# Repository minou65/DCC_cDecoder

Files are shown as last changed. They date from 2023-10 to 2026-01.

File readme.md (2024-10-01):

# cDecoder
## Inhalt
- [cDecoder](#cdecoder)
  - [Inhalt](#inhalt)
  - [Funktionen](#funktionen)
  - [Programmierung](#programmierung)
  - [Analog Betrieb](#analog-betrieb)
  - [Immer ein](#immer-ein)
  - [Powerpack](#powerpack)
  - [Dimmen der Ausgänge](#dimmen-der-ausgänge)
  - [Anschlüsse](#anschlüsse)
    - [fDecoder](#fdecoder)
    - [cDecoder](#cdecoder-1)
    - [PowerPack](#powerpack-1)
    - [Farben](#farben)
  - [Lange DCC Adresse](#lange-dcc-adresse)
  - [CV Tabelle](#cv-tabelle)
    - [Zuordnung Ausgänge zu Funktionstasten](#zuordnung-ausgänge-zu-funktionstasten)
    - [Funktion aktiv bei](#funktion-aktiv-bei)
    - [Modus der Ausgänge](#modus-der-ausgänge)
      - [Blinker On Time](#blinker-on-time)
      - [Blinker off Time](#blinker-off-time)
      - [Dimmen der Ausgänge](#dimmen-der-ausgänge-1)
      - [Automatisches abschalten](#automatisches-abschalten)
  - [Beispiele](#beispiele)
  - [Programmieren des prozessors](#programmieren-des-prozessors)

## Funktionen
- Ein/Aus
- Impuls
- Blinker

Der Attiny85 untersützt nur 5 Ausgänge. Die Funktionen sind auf die Ausgänge verteilt. Die Funktionen können über die CV's 66 - 70 eingestellt werden. 
Die Blinkerfunktion kann über die CV's 71 - 75 eingestellt werden. Die Zeit für das Blinken kann über die CV's 76 - 80 eingestellt werden. 
Die Zeit wird in 10ms Schritten angegeben. Die Helligkeit der Ausgänge kann über die CV's 81 und 82 eingestellt werden. 
Die Zeit für das automatische abschalten kann über die CV's 86 - 90 eingestellt werden. Die Zeit wird in 10ms Schritten angegeben.

## Programmierung
Um den Decoder auf dem Programmiergleis programmieren zu können muss eine Last an AUX 1 angeschlossen werden, die mindestens einen Strom von 60mA erzeugt.

## Analog Betrieb
Wird während 100ms kein DCC Signal erkannt, werden die Funktionen gemäss CV 13 aktiviert

## Immer ein
Ab Version 3 untersützt die Firmware CV 123, damit können Ausgänge definiert werden, welche beim anlagen einer Spannung sofort eingeschaltet werden.
Eingeführt für die Rheinbrücke beim Modell Eisenbahn Club Seebezirk (MECS), Fräschels (CH)

## Powerpack
Ein externes Powerpack kann an den Decoder angeschlossen werden. Dazu können die Pad's VCC und GND auf der Rückseite des Decoders verwendet werden.

## Dimmen der Ausgänge
Die Ausgänge AUX 1 und AUX 2 können gedimmt werden. Die Helligkeit kann über CV 81 und 82 eingestellt werden.

## Anschlüsse
### fDecoder
| oben | unten |
|---|---|
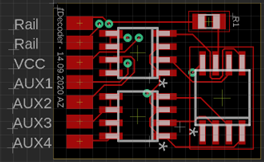
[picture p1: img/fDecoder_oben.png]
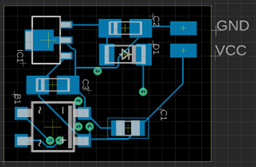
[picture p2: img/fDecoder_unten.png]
|  |  |
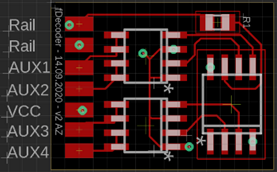
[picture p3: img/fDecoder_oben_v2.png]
| __v2__ <br>  | |

### cDecoder
| oben | unten |
|---|---|
| ||

### PowerPack
| oben | unten |
|---|---|
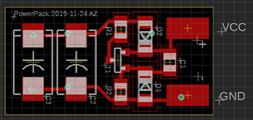
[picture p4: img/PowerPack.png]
|  ||

### Farben
| Draht | Verwendung |
|---|---|
| Rot | Rail |
| Braun | Rail |
| Blau | Decoder + |
| Weiss | Aux 1 / Licht vorne |
| Gelb | Aux 2 / Licht hinten |
| Violett | Aux 3 |
| Grün | Aux 4 |
| Schwarz | GND |

## Lange DCC Adresse
Um die lange DCC-Adresse in die Register 17 und 18 umzurechnen, kann folgende Formel verwendet werden.<br><br>
CV 17 = Adresse / 256 (nur die Stellen vor dem Komma) + 192<br>
CV 18 = Adresse - ((CV 17 - 192) * 256)<br>

Die lange Adresse wird nur verwendet, wenn das Bit 5 in CV 29 gesetzt ist

Hier gibt es einen CV Rechner
https://www.opendcc.de/info/decoder/dcc_cv.html

## CV Tabelle
| Bezeichnung | CV | Wertbereich <br> (default) | Beschreibung |
|---|:---:|---|---|
| Basisadresse | 1 | 1 - 255 (3) | Wertebereich im DCC-Format 1 - 127 |
| | 2 | 120 | |
| | 5 | 255 | |
| Version | 7 | | |
| Hersteller | 8 | | |
| Reset | 8 |  | Durch Eingeben eines Wertes 8, werden alle Einstellungen auf Default gesetzt |
| Im Analogbetrieb aktive Ausgänge | 13 | 0 - 255 (0) | AUX 1 ein = 1<br>AUX 2 ein = 2<br>AUX 3 ein = 4<br>AUX 4 ein = 8<br>AUX 5 ein = 16 |
| Decoderlock | 15 | 0 - 255 (0) | Decoder-Lock Funktion laut NMRA. <br>Details siehe http://www.nmra.org/standards/DCC/WGpublic/0305051/0305051.html |
| Decoderlock | 16 | 0 - 255 (0) | Decoder-Lock Funktion laut NMRA. <br>Details siehe http://www.nmra.org/standards/DCC/WGpublic/0305051/0305051.html |
| Erweiterte Adresse | 17 | 192 - 255 (0) | Nur für DCC-Format. Bei den meisten Zentralen ist es möglich, <br> erweiterte Adressendirekt einzugeben. Die CVs 17, 18 und 29 <br> werden von der Zentrale automatisch richtig eingestellt. |
| Erweiterte Adresse | 18 | 0 - 255 (3) |
| Konfigurationsdaten | 29 | 0 - 64 (2) | Fahrtrichtung Standard = 0 <br>Fahrtrichtung invertiert = 1 <br>14 Fahrstufen = 0 <br>28 oder 128 Fahrstufen 2 <br>Basisadressen = 0 <br>Erweiterte Adressen = 32 |
| Betriebszustand | 122 | 0/1 (0) | Den Betriebszustand der Ausgänge speichern. <br>0 = Aus <br>1 = Ein |
| Immer eingeschaltet<br>(ab Version 3) | 123 | 0 - 255 (0) | AUX 1 ein = 1<br>AUX 2 ein = 2<br>AUX 3 ein = 4<br>AUX 4 ein = 8<br>AUX 5 ein = 16 |

### Zuordnung Ausgänge zu Funktionstasten
| Bezeichnung | CV | Wertbereich <br> (default) | Beschreibung |
|---|:---:|---|---|
| F0 | 30 | 0 - 31 (3) | AUX 1 = 1 <br> AUX 2 = 2 <br> AUX 3 = 4 <br> AUX 4 = 8 <br> AUX 5 = 16 |
| F1 | 31 | 0 - 31 (4) | |
| F2 | 32 | 0 - 31 (8) | |
| ... | ... | 0 - 31 (0) | |
| F28 | 58 | 0 - 31 (0) | |

### Funktion aktiv bei
| Bezeichnung | CV | Wertbereich <br> (default) | Beschreibung |
|---|:---:|---|---|
| AUX 1 | 61 | 0 - 31 (1) | Vorwärts = 0 <br> Rückwärts = 1 <br> Beide = 3 <br> Default bei cDecoder ist 3 |
| AUX 2 | 62 | 0 - 31 (2) | Default bei cDecoder ist 3 |
| AUX 3 | 63 | 0 - 31 (3) | |
| AUX 4 | 64 | 0 - 31 (3) | |
| AUX 5 | 65 | 0 - 31 (3) | |

### Modus der Ausgänge
| Bezeichnung | CV | Wertbereich <br> (default) | Beschreibung |
|---|:---:|---|---|
| AUX 1 | 66 | 0 - 31 (1) | Ein / Aus = 1 <br> Blinker = 2 <br> Impuls = 3 |
| AUX 2 | 67 | 0 - 31 (1) | |
| AUX 3 | 68 | 0 - 31 (1) | |
| AUX 4 | 69 | 0 - 31 (2) | |
| AUX 5 | 70 | 0 - 31 (2) | |

#### Blinker On Time
| Bezeichnung | CV | Wertbereich <br> (default) | Beschreibung |
|---|:---:|---|---|
| AUX 1 | 71 | 0 - 255 (100) | Wert x 10 = Zeit in milli Sekunden |
| AUX 2 | 72 | 0 - 255 (100) | |
| AUX 3 | 73 | 0 - 255 (100) | |
| AUX 4 | 74 | 0 - 255 (100) | |
| AUX 5 | 75 | 0 - 255 (100) | |

#### Blinker off Time
| Bezeichnung | CV | Wertbereich <br> (default) | Beschreibung |
|---|:---:|---|---|
| AUX 1 | 76 | 0 - 255 (100) | Wert x 10 = Zeit in milli Sekunden |
| AUX 2 | 77 | 0 - 255 (100) | |
| AUX 3 | 78 | 0 - 255 (100) | |
| AUX 4 | 79 | 0 - 255 (100) | |
| AUX 5 | 80 | 0 - 255 (100) | |

#### Dimmen der Ausgänge
| Bezeichnung | CV | Wertbereich <br> (default) | Beschreibung |
|---|:---:|---|---|
| AUX 1 | 81 | 1 - 255 (255) | |
| AUX 2 | 82 | 1 - 255 (255) | |

#### Automatisches abschalten
| Bezeichnung | CV | Wertbereich <br> (default) | Beschreibung |
|---|:---:|---|---|
| AUX 1 | 86 | 0 - 255 (0) | Wert x 10 = Zeit in milli Sekunden. Ist der <br> Wert grösser als 0 wird der Ausgang nach der <br> eingestellten Zeit wieder abgeschaltet. <br> Ist der Wert 0, dann bleibt der Ausgang eingeschaltet. |
| AUX 2 | 87 | 0 - 255 (0) | |
| AUX 3 | 88 | 0 - 255 (0) | |
| AUX 4 | 89 | 0 - 255 (0) | |
| AUX 5 | 90 | 0 - 255 (0) | |

## Beispiele
|Beispiel | Einstellungen |
|---|---|
| SBB Schlusslicht an AUX 4 <br><br><br><br> | CV64 = 36<br>CV69 = 27 <br>CV74 = 1 (On Time)<br>CV79 = 70 (Off Time) |
| Rheinbrücke MESC<br>Rote LED soll immer blinken<br><br><br> | CV123 = 1<br>CV66 = 2<br>CV71 = 80<br>76 = 20 |

## Programmieren des prozessors

Um den Prozessor zu programmieren wird ein ISP Programmer benötigt. Der Prozessor kann mit der Arduino IDE programmiert werden. Dazu muss der Prozessor als Board hinzugefügt werden.
- Dazu unter Datei -> Voreinstellungen -> Zusätzliche Boardverwalter-URLs: https://raw.githubusercontent.com/damellis/attiny/ide-1.6.x-boards-manager/package_damellis_attiny_index.json einfügen.
- Arduino AVR Boards installieren unter Werkzeuge -> Board -> Boardverwalter... -> Arduino AVR Boards installieren.
- In der Arduino IDE unter Werkzeuge -> Board -> Boardverwalter... -> attiny auswählen und installieren. 

Danach das Board wie folgt konfigurieren
    Board    : Attiny25/45/85
    Prozessor: Attiny85
    Clock    : Internal 16Mhz
    Programmer: Diamex USB ISP oder ATMEL STK500 (Für Windows 10 ist kein Treiber erforderlich)

Nun kann zuerst der Bootloader und danach die Firmware auf den Prozessor geschrieben werden. Unter visual Micro kommt folgende Fehlermeldung beim schreiben des Bootloaders

```
Error while burning bootloader.
Burn failed
avrdude: can't open input file aders/{bootloader.file}: No such file or directory
avrdude: read from file oaders/{bootloader.file}' failed
```

Dies ist normal, der Attiny hat keine Bootloader visual Micro sucht diesen aber und findet ihn nicht. Die Fuse und Clock settings werden aber geschrieben bevor der Bootloader geschrieben wird.
https://www.visualmicro.com/forums/YaBB.pl?num=1607630288

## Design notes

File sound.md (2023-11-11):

# Sound Decoder

Der Sounddecoder besitzt nur 3 Ausgänge, davon sind 2 mit PWM.

## Inhalt
- [Sound Decoder](#sound-decoder)
  - [Inhalt](#inhalt)
  - [Verzeichnis MP3](#verzeichnis-mp3)
  - [Verzeichnis ADVERT](#verzeichnis-advert)
  - [Erweiterte CV Tabelle](#erweiterte-cv-tabelle)
    - [Einstellungen](#einstellungen)
    - [Zuordnung Sound zu Funktionstasten](#zuordnung-sound-zu-funktionstasten)

## Verzeichnis MP3

Dieses Verzeichnis muss exakt als __MP3__ benannt werden. Hier passen bis zu 3000 Dateien mit dem Namensschema 0001.mp3 (bzw. wav), 0002.mp3, ….. 3000.mp3 hinein.

Möglich ist es auch die Dateien 0001-Lokpiff.mp3 zu benennen. Auch Leerzeichen sind erlaubt.

## Verzeichnis ADVERT

Es gelten dieselben Regeln wie für das MP3 Verzeichnis. Das ADVERT Verzeichnis hat eine besondere Funktion. Spielt man eine Datei aus einem der anderen Verzeichnisse ab und ruft währenddessen eine Datei aus dem ADVERT Verzeichnis auf, so wird das Abspielen der ursprünglichen Datei lediglich unterbrochen. Nach dem Beenden der ADVERT Einspielung wird das ursprüngliche Stück fortgesetzt. Es ist wie eine Werbeeinblendung und so deutet es der Name des Verzeichnisses ja auch schon an.

## Erweiterte CV Tabelle

### Einstellungen
| Bezeichnung | CV | Wertbereich <br> (default) | Beschreibung |
|---|:---:|---|---|
| Volume | 125 | 0 - 30 (10) | Lautstärke |
| EQ | 126 | 0 - 5 (0) | 0 = Normal <br> 1 = POP <br> 2 = Rock <br> 3 = Jazz <br> 4 = Classic <br> 5 = Bass |

### Zuordnung Sound zu Funktionstasten
| Bezeichnung | CV | Wertbereich <br> (default) | Beschreibung |
|---|:---:|---|---|
| F0 | 130 | 0 - 255 (0) | 0 = kein Sound <br> 1 - 255 = Nummer des Sounds der gespielt werden soll. <br><br> Dabei gilt: <br> 1 - 100, dieser Sound wir aus dem Verzeichnis MP3 abgespielt. <br> 101 - 200, dieser Sound wird aus dem Verzeichnis ADVERT abgespielt. <br> 201 - 240, dieser Sound wird aus dem Verzeichnis MP3 in einem Loop abgespielt. <br> 250 = Mute / Unmute <br> 251 = Volume up <br> 252 = Volume down <br><br> Die Dateien müssen auch jeweils die entsprechende Nummer besitzen. |
| ... | ... | 0 - 255 (0) | |
| F10 | 140 | 0 - 255 (250) | Mute / Unmute |
| F11 | 141 | 0 - 255 (251) | Volume up |
| F12 | 142 | 0 - 255 (252) | Volume down |
| F28 | 158 | 0 - 255 (0) | |

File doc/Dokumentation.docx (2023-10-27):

# Funktionsdecoder

## Funktionen

- Ein/Aus
- Impuls
- Blinker

## Programmierung

Um den Decoder auf dem Programmiergleis programmieren zu können muss eine Last an AUX 1 angeschlossen werden, die mindestens einen Strom von 60mA erzeugt.

## Analog betrieb

Wird während 100ms kein DCC Signal erfasst, werden die Funktionen gemäss CV 13 aktiviert

## Powerpack

Ein externes Powerpack kann an den Decoder angeschlossen werden. Dazu können die Pad’s VCC und GND auf der Rückseite des Decoders verwendet werden.

## Dimmen der Ausgänge

Die Ausgänge AUX 1 und AUX 2 können gedimmt werden. Die Helligkeit kann über CV 81 und 82 eingestellt werden.

## Anschlüsse

## fDecoder

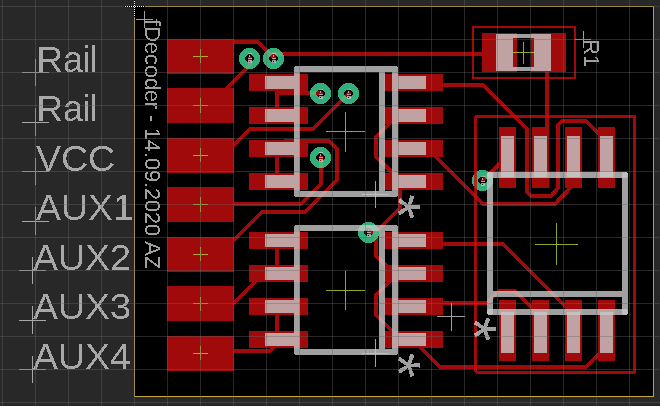
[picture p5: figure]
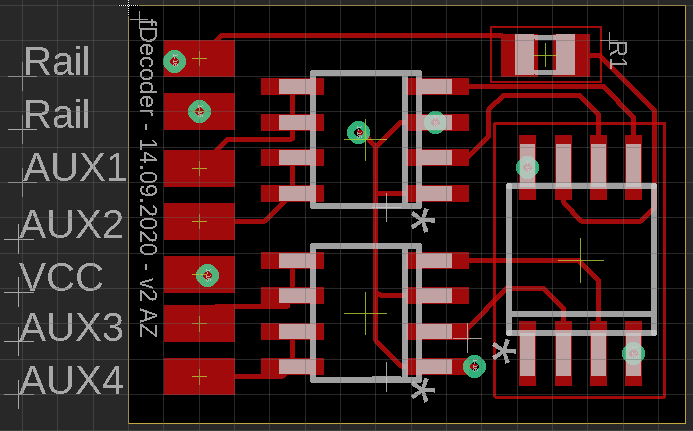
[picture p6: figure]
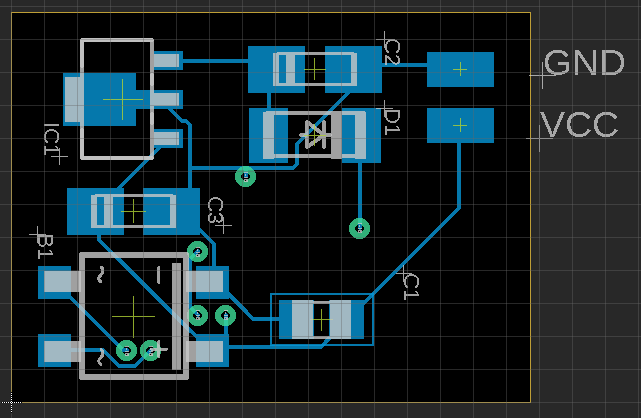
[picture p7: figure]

V2

## cDecoder

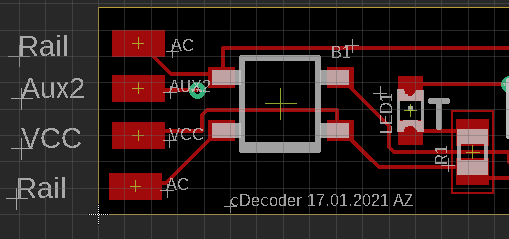
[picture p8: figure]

## PowerPack

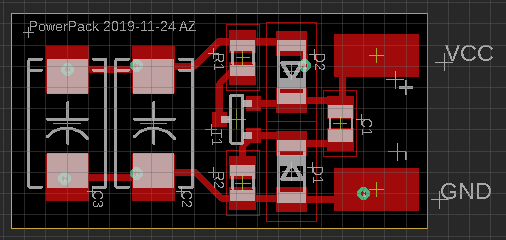
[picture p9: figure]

## Farben

Rot | Rail
Braun | Rail
Blau | Decoder +
Weiss | Aux 1 / Licht vorne
Gelb | Aux 2 / Licht hinten
Violett | Aux 3
Grün | Aux 4
Schwarz | GND

## CV Tabelle

Basisadresse | 1 | 1 – 255 (3) | Wertebereich im DCC-Format 1 – 127
| 2 | 120
| 5 | 255
Version | 7
Hersteller | 8
Reset | 8 | | Durch Eingeben eines Wertes 8, werden alle Einstellungen auf Default gesetzt
Im Analogbetrieb aktive Ausgänge | 13 | 0 – 255 (0) | AUX 1 ein = 1 AUX 2 ein = 2 AUX 3 ein = 4 AUX 4 ein = 8 AUX 5 ein = 16
Decoderlock | 15 16 | 0 – 255 (0) | Decoder-Lock Funktion laut NMRA. Details siehe http://www.nmra.org/standards/DCC/WGpublic/0305051/0305051.html
Erweiterte Adresse | 17 | 192 – 255 (0) | Nur für DCC-Format. Bei den meisten Zentralen ist es möglich, erweiterte Adressen direkt einzugeben. Die CVs 17, 18 und 29 werden von der Zentrale automatisch richtig eingestellt.
| 18 | 0 – 255 (3)
Konfigurationsdaten | 29 | 0 – 64 (2) | Fahrtrichtung Standard = 0 Fahrtrichtung invertiert = 1 14 Fahrstufen = 0 28 oder 128 Fahrstufen 2 Basisadressen = 0 Erweiterte Adressen = 32
Betriebszustand | 122 | 0/1 (0) | Speicher den Betriebszustand der Ausgänge. 0 = Aus 1 = Ein

Zuordnung Ausgänge zu Funktionstasten
F0 | 30 | 0 – 31 (3) | AUX 1 = 1 AUX 2 = 2 AUX 3 = 4 AUX 4 = 8 AUX 5 = 16
F1 | 31 | 0 – 31 (4)
F2 | 32 | 0 – 31 (8)
… | | 0 – 31 (0)
F28 | 58 | 0 – 31 (0)

Funktion aktiv bei :
AUX 1 | 61 | 0 – 31 (1) | Vorwärts = 1 Rückwärts = 2 Beide = 3 Default bei cDecoder ist 3
AUX 2 | 62 | 0 – 31 (2) | Default bei cDecoder ist 3
AUX 3 | 63 | 0 – 31 (3)
AUX 4 | 64 | 0 – 31 (3)
AUX 5 | 65 | 0 – 31 (3)

Modus :
AUX 1 | 66 | 0 – 31 (1) | Ein / Aus = 1 Blinker = 2 Impuls = 3
AUX 2 | 67 | 0 – 31 (1)
AUX 3 | 68 | 0 – 31 (1)
AUX 4 | 69 | 0 – 31 (2)
AUX 5 | 70 | 0 – 31 (2)

Blinker On Time
AUX 1 | 71 | 0 – 255 (100) | Wert x 10 = Zeit in milli Sekunden
AUX 2 | 72 | 0 – 255 (100)
AUX 3 | 73 | 0 – 255 (100)
AUX 4 | 74 | 0 – 255 (100)
AUX 5 | 75 | 0 – 255 (100)

Blinker Off Time
AUX 1 | 76 | 0 – 255 (100) | Wert x 10 = Zeit in milli Sekunden
AUX 2 | 77 | 0 – 255 (100)
AUX 3 | 78 | 0 – 255 (100)
AUX 4 | 79 | 0 – 255 (100)
AUX 5 | 80 | 0 – 255 (100)

Dimmen der Ausgänge
AUX 1 | 81 | 1 – 255 (255)
AUX 2 | 82 | 1 – 255 (255)

Automatisches abschalten
AUX 1 | 86 | 0 – 255 (0) | Wert x 10 = Zeit in milli Sekunden. Ist der Wert grösser als 0 wird der Ausgang nach der eingestellten Zeit wieder abgeschaltet. Ist der Wert 0, dann bleibt der Ausgang eingeschaltet.
AUX 2 | 87 | 0 – 255 (0)
AUX 3 | 88 | 0 – 255 (0)
AUX 4 | 89 | 0 – 255 (0)
AUX 5 | 90 | 0 – 255 (0)

Datenspeicherung
Zustand der Funktionstasten speichern | 122 | 0 / 1 (0)

# Sound Decoder

Der Sounddecoder besitzt nur 3 Ausgänge, davon sind 2 mit PWM.

## Verzeichnis MP3

Dieses Verzeichnis muss exakt als „MP3“ benannt werden. Hier passen bis zu 3000 Dateien mit dem Namensschema 0001.mp3 (bzw. wav), 0002.mp3, ….. 3000.mp3 hinein.

Möglich ist es auch die Dateien 0001-Lokpiff.mp3 zu benennen. Auch Leerzeichen sind erlaubt.

## Verzeichnis ADVERT

Es gelten dieselben Regeln wie für das MP3 Verzeichnis. Das ADVERT Verzeichnis hat eine besondere Funktion. Spielt man eine Datei aus einem der anderen Verzeichnisse ab und ruft währenddessen eine Datei aus dem ADVERT Verzeichnis auf, so wird das Abspielen der ursprünglichen Datei lediglich unterbrochen. Nach dem Beenden der ADVERT Einspielung wird das ursprüngliche Stück fortgesetzt. Es ist wie eine Werbeeinblendung und so deutet es der Name des Verzeichnisses ja auch schon an.

## Erweiterte CV Tabelle

Einstellungen
Volume | 125 | 0 – 30 (10) | Volume
EQ | 126 | 0 – 5 (0) | 0 = Normal 1 = POP 2 = Rock 3 = Jazz 4 = Classic 5 = Bass

Zuordnung Sound zu Funktionstasten
F0 | 130 | 0 – 255 (0) | 0 = kein Sound, 1 – 255 = Nummer des Sounds der gespielt werden soll. Dabei gilt: - 1 – 100, dieser Sound wir aus dem Verzeichnis MP3 abgespielt. - 101 – 200, dieser Sound wird aus dem Verzeichnis ADVERT abgespielt. - 201 – 240, dieser Sound wird aus dem Verzeichnis MP3 in einem Loop abgespielt. - 250 = Mute / Unmute - 251 = Volume up - 252 = Volume down Die Dateien müssen auch jeweils die entsprechende Nummer besitzen.
… | … | 0 – 255 (0)
F10 | 140 | 0 – 255 (250) | Mute / Unmute
F11 | 141 | 0 – 255 (251) | Volume up
F12 | 142 | 0 – 255 (252) | Volume down
F28 | 158 | 0 – 255 (0)

## Beispiele

SBB Schlusslicht an AUX 4 | 64 = 3 69 = 2 74 = 1 (On Time) 79 = 70 (Off Time)

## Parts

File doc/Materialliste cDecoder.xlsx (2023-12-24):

Bauteil | Bestellnummer | Lieferant
Printplatte |  | PCB | CHF 1.50
LED1 |  |  | CHF 0.10
LED2 |  |  | CHF 0.10
LED3 |  |  | CHF 0.10
LED4 |  |  | CHF 0.10
LED5 |  |  | CHF 0.10
LED6 |  |  | CHF 0.10
LED7 |  |  | CHF 0.10
LED8 |  |  | CHF 0.10
LED9 |  |  | CHF 0.10
LED10 |  |  | CHF 0.10
R1 |  |  | CHF 0.10
R2 |  |  | CHF 0.10
R3 |  |  | CHF 0.10
R4 |  |  | CHF 0.10
R5 |  |  | CHF 0.10
R6 |  |  | CHF 0.10
R7 |  |  | CHF 0.10
R8 |  |  | CHF 0.10
R9 |  |  | CHF 0.10
R10 |  |  | CHF 0.10
B1 | RECTIFIER-S80 |  | CHF 0.25
C1 | 10u |  | CHF 0.10
D1 | 1N4148W |  | CHF 0.10
IC1 | L78L05ACUTR |  | CHF 0.10
T1 | SI9945BDY |  | CHF 0.55
U1 | ATTINY85-20S |  | CHF 4.00
Summe |  |  | CHF 8.60

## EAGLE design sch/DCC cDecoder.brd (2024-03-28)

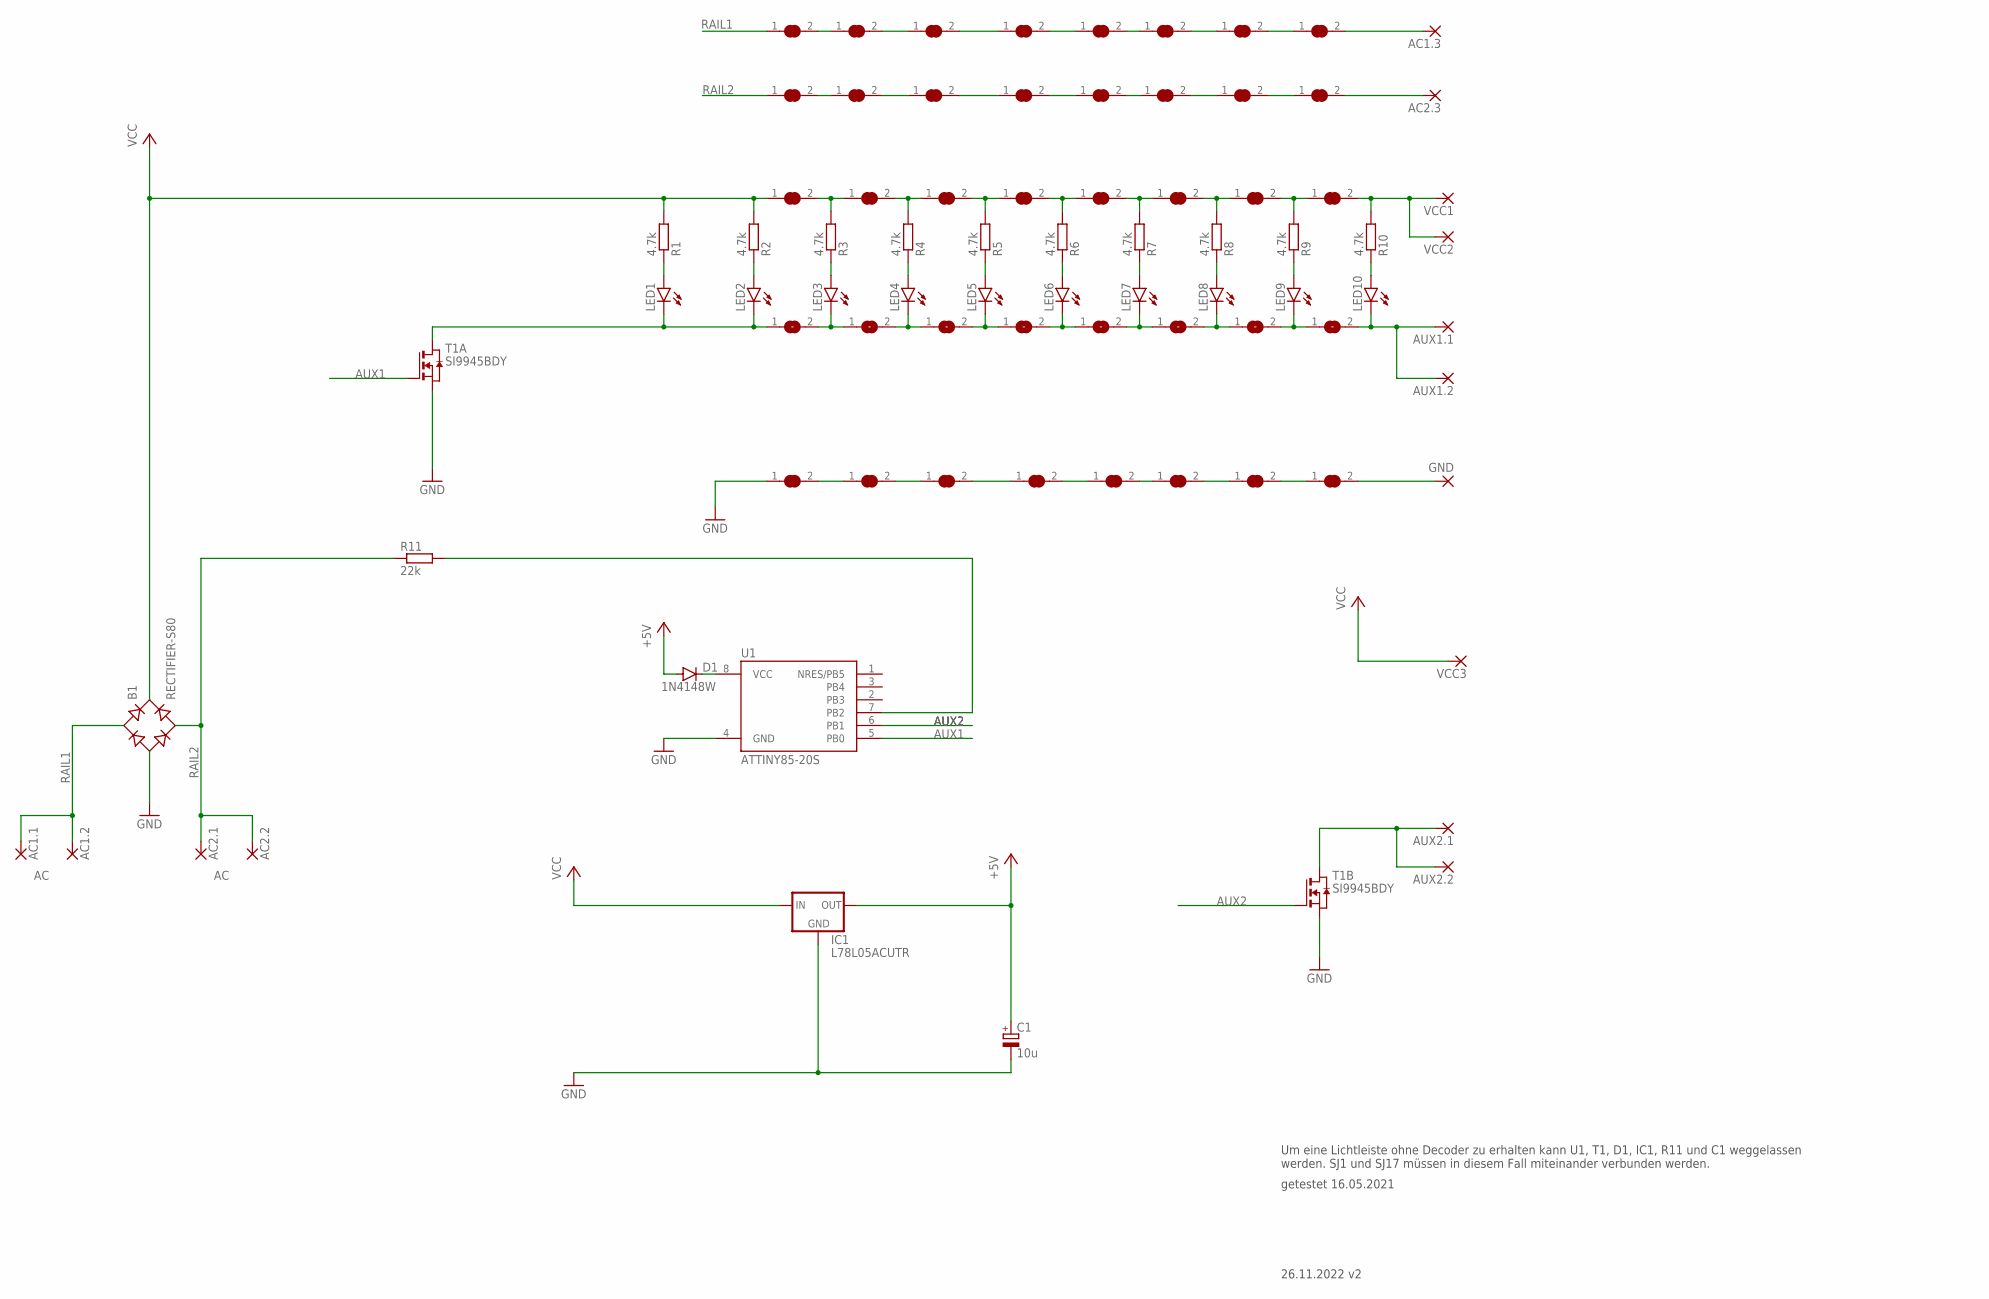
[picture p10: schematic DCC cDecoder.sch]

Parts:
AC1.1: AC1.1; SMD1,27-2,54
AC1.2: AC1.2; SMD1,27-2,54
AC1.3: AC1.3; SMD1,27-2,54
AC2.1: AC2.1; SMD1,27-2,54
AC2.2: AC2.2; SMD1,27-2,54
AC2.3: AC2.3; SMD1,27-2,54
AUX1.1: AUX1.1; SMD1,27-2,54
AUX1.2: AUX1.2; SMD1,27-2,54
AUX2.1: AUX2.1; SMD1,27-2,54
AUX2.2: AUX2.2; SMD1,27-2,54
B1: RECTIFIER-S80; TO-269AA
C1: 10u; A/3216-18W
D1: 1N4148W; SOD-123_MINI-SMA
GND: SMD2; SMD1,27-2,54
IC1: L78L05ACUTR; SOT89R
LED1, LED2, LED3, LED4, LED5, LED6, LED7, LED8, LED9, LED10: LEDCHIPLED_0805; CHIPLED_0805
R1, R2, R3, R4, R5, R6, R7, R8, R9, R10: 4.7k; R0805
R11: 22k; R0805
SJ1, SJ2, SJ3, SJ4, SJ5, SJ6, SJ7, SJ8, SJ9, SJ10, SJ11, SJ12, SJ13, SJ14, SJ15, SJ16, SJ25, SJ26, SJ27, SJ28, SJ29, SJ30, SJ31, SJ32, SJ33, SJ34, SJ35, SJ36, SJ37, SJ38, SJ39, SJ40: SJC
SJ17, SJ18, SJ19, SJ20, SJ21, SJ22, SJ23, SJ24: SJ
T1: SI9945BDY; SO8
U1: ATTINY85-20S; SOIC8_EIAJ_208MIL
VCC1: VCC1; SMD1,27-2,54
VCC2: VCC2; SMD1,27-2,54
VCC3: VCC3; SMD1,27-2,54

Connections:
+5V: C1.+, D1.A, IC1.2 (OUT)
AUX1: T1.2 (G), U1.5 (PB0)
AUX2: T1.4 (G), U1.6 (PB1)
GND: B1.-, C1.-, IC1.3 (GND), IC1.4 (GND), SJ1.1, T1.1 (S), T1.3 (S), U1.4 (GND)
unnamed: LED2.A, R2.1
unnamed: LED1.A, R1.1
unnamed: R3.2, SJ2.2, SJ4.1
unnamed: LED4.A, R4.1
unnamed: LED3.A, R3.1
unnamed: R6.2, SJ8.2, SJ10.1
unnamed: R7.2, SJ10.2, SJ12.1
unnamed: R8.2, SJ12.2, SJ14.1
unnamed: R9.2, SJ14.2, SJ16.1
unnamed: LED6.A, R6.1
unnamed: SJ1.2, SJ3.1
unnamed: R4.2, SJ4.2, SJ6.1
unnamed: LED7.A, R7.1
unnamed: LED8.A, R8.1
unnamed: AUX2.1.1, AUX2.2.1, T1.5 (D), T1.6 (D)
unnamed: SJ3.2, SJ5.1
unnamed: R5.2, SJ6.2, SJ8.1
unnamed: SJ5.2, SJ7.1
unnamed: LED3.C, SJ17.2, SJ18.1
unnamed: SJ7.2, SJ9.1
unnamed: LED5.A, R5.1
unnamed: SJ9.2, SJ11.1
unnamed: LED4.C, SJ18.2, SJ19.1
unnamed: SJ11.2, SJ13.1
unnamed: LED9.A, R9.1
unnamed: SJ13.2, SJ15.1
unnamed: LED10.A, R10.1
unnamed: GND.1, SJ15.2
unnamed: LED6.C, SJ20.2, SJ21.1
unnamed: D1.C, U1.8 (VCC)
unnamed: R10.2, SJ16.2, VCC1.1, VCC2.1
unnamed: LED5.C, SJ19.2, SJ20.1
unnamed: R11.2, U1.7 (PB2)
unnamed: AUX1.1.1, AUX1.2.1, LED10.C, SJ24.2
unnamed: LED7.C, SJ21.2, SJ22.1
unnamed: LED8.C, SJ22.2, SJ23.1
unnamed: LED9.C, SJ23.2, SJ24.1
unnamed: LED1.C, LED2.C, SJ17.1, T1.7 (D), T1.8 (D)
unnamed: SJ25.2, SJ26.1
unnamed: SJ26.2, SJ27.1
unnamed: SJ27.2, SJ28.1
unnamed: SJ28.2, SJ29.1
unnamed: SJ29.2, SJ30.1
unnamed: SJ30.2, SJ31.1
unnamed: SJ31.2, SJ32.1
unnamed: AC1.3.1, SJ32.2
unnamed: SJ33.2, SJ34.1
unnamed: SJ34.2, SJ35.1
unnamed: SJ35.2, SJ36.1
unnamed: SJ36.2, SJ37.1
unnamed: SJ37.2, SJ38.1
unnamed: SJ38.2, SJ39.1
unnamed: SJ39.2, SJ40.1
unnamed: AC2.3.1, SJ40.2
RAIL1: AC1.1.1, AC1.2.1, B1.AC1, SJ25.1
RAIL2: AC2.1.1, AC2.2.1, B1.AC2, R11.1, SJ33.1
VCC: B1.+, IC1.1 (IN), R1.2, R2.2, SJ2.1, VCC3.1

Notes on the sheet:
getestet 16.05.2021
Um eine Lichtleiste ohne Decoder zu erhalten kann U1, T1, D1, IC1, R11 und C1 weggelassen werden. SJ1 und SJ17 müssen in diesem Fall miteinander verbunden werden.
26.11.2022 v2

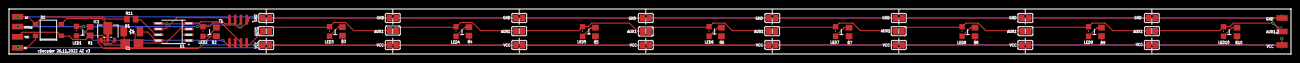
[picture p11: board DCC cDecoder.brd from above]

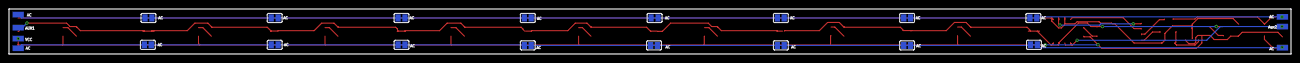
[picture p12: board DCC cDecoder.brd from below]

Board: 2 copper layers, 285.0 x 10.0 mm, 81 parts (23 on the bottom side), 61 nets.

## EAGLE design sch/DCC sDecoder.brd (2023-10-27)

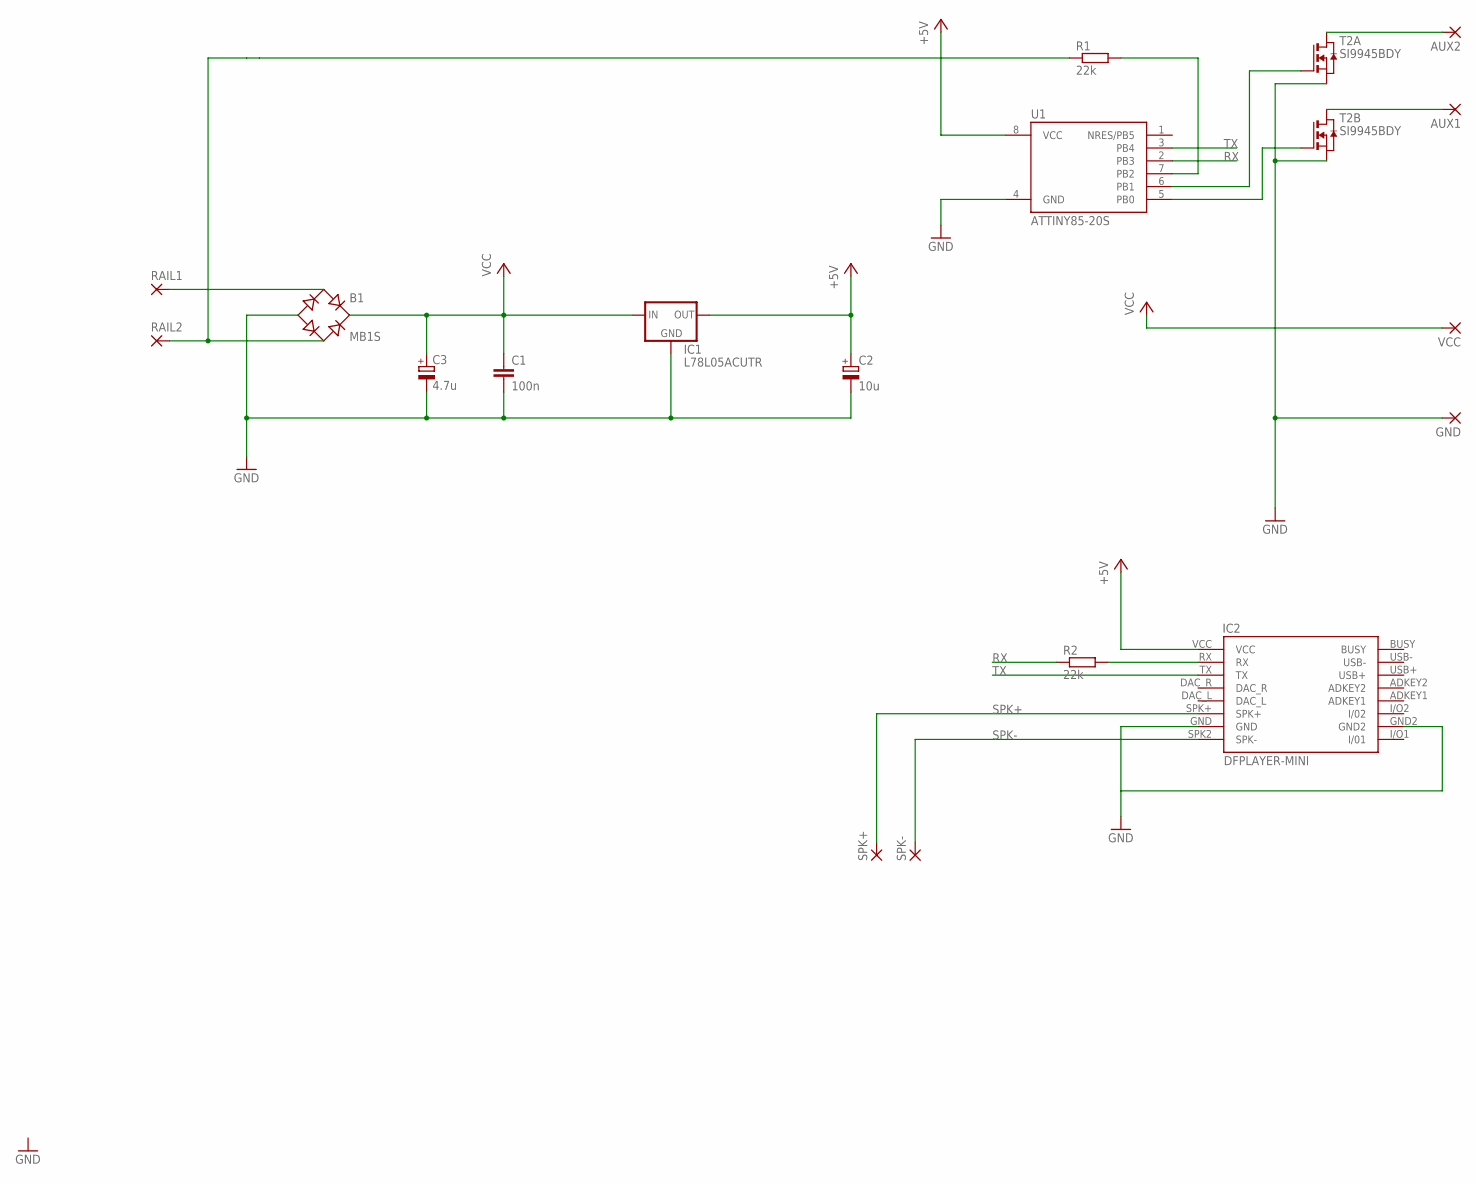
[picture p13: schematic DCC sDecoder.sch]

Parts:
AUX1, AUX2: SMD2; SMD1,27-2,54
B1: MB1S; SOIC-4
C1: 100n; C0805
C2: 10u; A/3216-18W
C3: 4.7u; A/3216-18W
GND: SMD2; SMD1,27-2,54
IC1: L78L05ACUTR; SOT89R
IC2: DFPLAYER-MINI
R1, R2: 22k; R0805
RAIL1, RAIL2: SMD2; SMD1,27-2,54
SPK+: SMD2; SMD1,27-2,54
SPK-: SMD2; SMD1,27-2,54
T2: SI9945BDY; SO8
U1: ATTINY85-20S; SOIC8_EIAJ_208MIL
VCC: SMD2; SMD1,27-2,54

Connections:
+5V: C2.+, IC1.2 (OUT), IC2.VCC, U1.8 (VCC)
GND: B1.-, C1.2, C2.-, C3.-, GND.1, IC1.3 (GND), IC1.4 (GND), IC2.GND, IC2.GND2, T2.1 (S), T2.3 (S), U1.4 (GND)
unnamed: IC2.RX, R2.2
unnamed: AUX2.1, T2.7 (D), T2.8 (D)
unnamed: AUX1.1, T2.5 (D), T2.6 (D)
unnamed: T2.4 (G), U1.5 (PB0)
unnamed: T2.2 (G), U1.6 (PB1)
unnamed: B1.~2 (AC2), R1.1, RAIL2.1
unnamed: R1.2, U1.7 (PB2)
unnamed: B1.~1 (AC1), RAIL1.1
RX: R2.1, U1.2 (PB3)
SPK+: IC2.SPK+, SPK+.1
SPK-: IC2.SPK2 (SPK-), SPK-.1
TX: IC2.TX, U1.3 (PB4)
VCC: B1.+, C1.1, C3.+, IC1.1 (IN), VCC.1

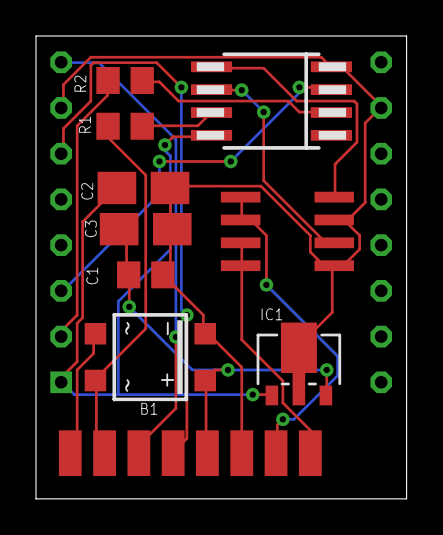
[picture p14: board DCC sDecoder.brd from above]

Board: 2 copper layers, 20.6 x 25.7 mm, 18 parts (1 on the bottom side), 15 nets.

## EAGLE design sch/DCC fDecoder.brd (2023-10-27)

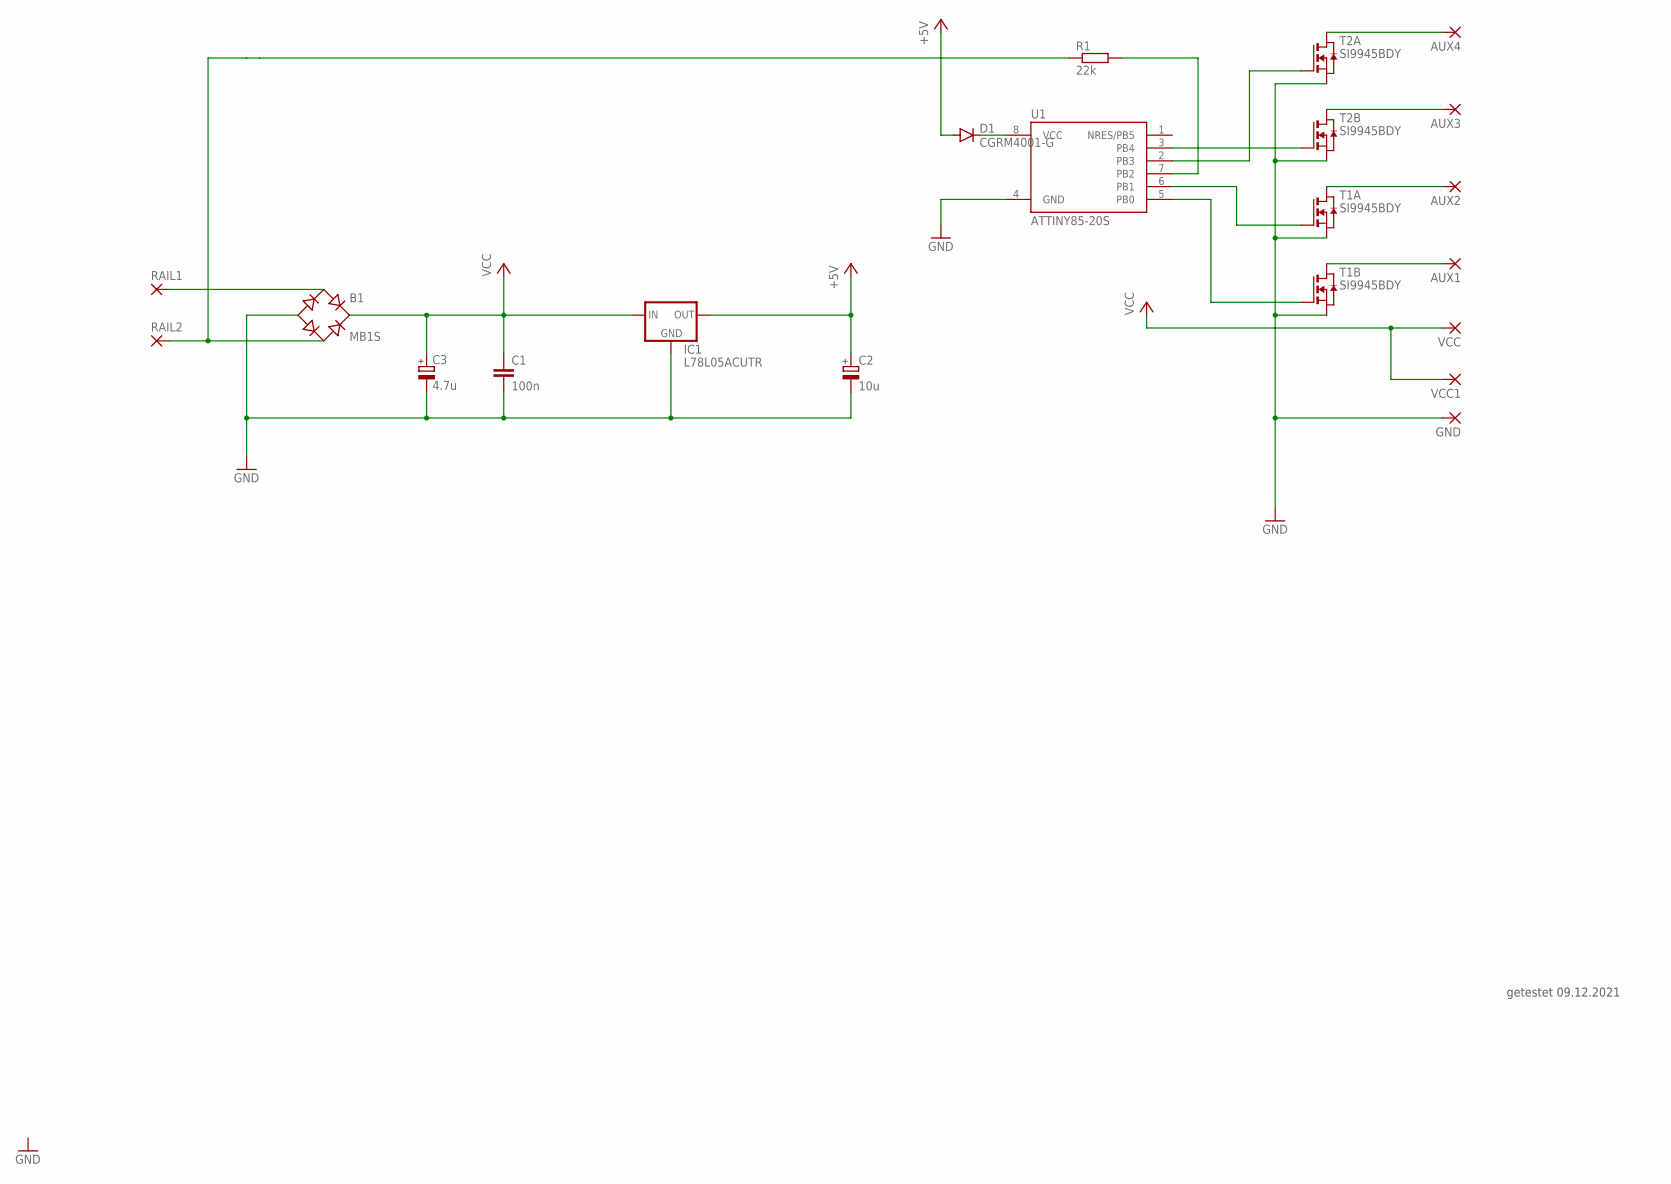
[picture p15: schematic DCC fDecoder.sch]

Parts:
AUX1, AUX2, AUX3, AUX4: SMD2; SMD1,27-2,54
B1: MB1S; SOIC-4
C1: 100n; C0805
C2: 10u; A/3216-18W
C3: 4.7u; A/3216-18W
D1: CGRM4001-G; SOD-123_MINI-SMA
GND: SMD2; SMD1,27-2,54
IC1: L78L05ACUTR; SOT89R
R1: 22k; R0805
RAIL1, RAIL2: SMD2; SMD1,27-2,54
T1, T2: SI9945BDY; SO8
U1: ATTINY85-20S; SOIC8_EIAJ_208MIL
VCC, VCC1: SMD2; SMD1,27-2,54

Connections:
+5V: C2.+, D1.A, IC1.2 (OUT)
GND: B1.-, C1.2, C2.-, C3.-, GND.1, IC1.3 (GND), IC1.4 (GND), T1.1 (S), T1.3 (S), T2.1 (S), T2.3 (S), U1.4 (GND)
unnamed: AUX1.1, T1.5 (D), T1.6 (D)
unnamed: AUX4.1, T2.7 (D), T2.8 (D)
unnamed: AUX3.1, T2.5 (D), T2.6 (D)
unnamed: AUX2.1, T1.7 (D), T1.8 (D)
unnamed: T1.4 (G), U1.5 (PB0)
unnamed: T1.2 (G), U1.6 (PB1)
unnamed: T2.2 (G), U1.2 (PB3)
unnamed: T2.4 (G), U1.3 (PB4)
unnamed: D1.C, U1.8 (VCC)
unnamed: B1.~2 (AC2), R1.1, RAIL2.1
unnamed: R1.2, U1.7 (PB2)
unnamed: B1.~1 (AC1), RAIL1.1
VCC: B1.+, C1.1, C3.+, IC1.1 (IN), VCC.1, VCC1.1

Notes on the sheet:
getestet 09.12.2021

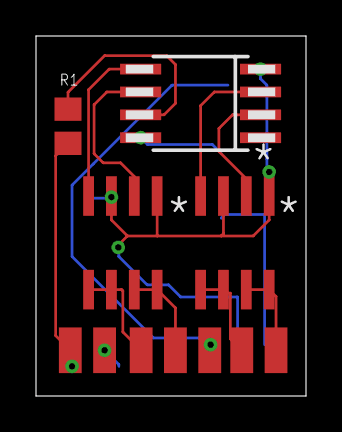
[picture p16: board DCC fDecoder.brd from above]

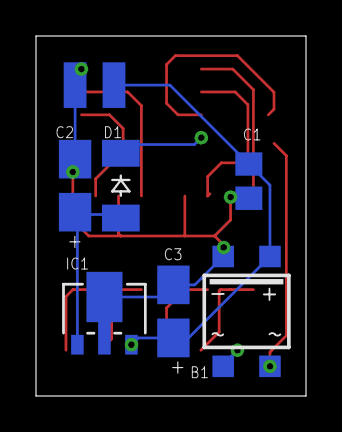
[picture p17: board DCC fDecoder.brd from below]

Board: 2 copper layers, 15.0 x 20.0 mm, 19 parts (8 on the bottom side), 15 nets.

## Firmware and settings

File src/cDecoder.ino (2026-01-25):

/*
 Name:		DCC_Funktionsdecoder.ino
 Created:	14.09.2020 10:22:04
 Author:	andy

 Bemerkungen:

siehe readme.md Programmieren des prozessors

*/

#include "DecoderCoreConfig.h"
#include "PinConfig.h"

// This is the version
#define DECODER_VERSION 4

// Default DCC Address
#define DEFAULT_DECODER_ADDRESS 3

#include "ATtiny_DecoderCore.h"

void setup() {

#ifdef LED_TEST 
    pinMode(LED_PIN_FWD, OUTPUT);
    pinMode(LED_PIN_REV, OUTPUT);
    pinMode(LED_PIN_AUX3, OUTPUT);
    pinMode(LED_PIN_AUX4, OUTPUT);


    digitalWrite(LED_PIN_FWD, HIGH);
    delay(1000);
    digitalWrite(LED_PIN_REV, HIGH);
    delay(1000);
    digitalWrite(LED_PIN_AUX3, HIGH);
    delay(500);
    digitalWrite(LED_PIN_AUX4, HIGH);
    delay(500);
    digitalWrite(LED_PIN_FWD, LOW);
    delay(500);
    digitalWrite(LED_PIN_REV, LOW);
    delay(500);
    digitalWrite(LED_PIN_AUX3, LOW);
    delay(500);
    digitalWrite(LED_PIN_AUX4, LOW);
    delay(500);
#endif // LED_TEST 
    setupDCC();
}

void loop() {
	loopDCC();
}

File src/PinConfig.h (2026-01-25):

// PinConfig.h

#ifndef _PINCONFIG_h
#define _PINCONFIG_h

#define DCC_PIN         2 
#define DCC_PIN_INT     PCINT2   // Interrupt number of the pin

#define LED_PIN_FWD     0   // AUX 1
#define LED_PIN_REV     1   // AUX 2
#define DCC_ACK_PIN     LED_PIN_FWD

#define NUM_OUTPUTS 2


#endif

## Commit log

2023-10-27 initial version
    [DCC cDecoder.brd, DCC cDecoder.sch, DCC fDecoder.brd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]
2023-12-04 version 2
    [DCC cDecoder.brd, DCC cDecoder.sch]
2023-12-24 layout v2
    [DCC cDecoder.brd]
2023-12-24 new file
    [Materialliste cDecoder.xlsx]
2024-03-28 footprint mosfet changed (v3)
    [DCC cDecoder.brd, DCC cDecoder.sch]
2024-03-29 fixed bug for analog mode
    [cDecoder.ino]
2024-03-30 fixed wrong function key bitmap for F5 - F9
    [cDecoder.ino]
2024-10-01 migratet to new version ESPAsyncWebServer. Added some error handling for more stability
    [CV Rechner.xlsx]
2026-01-25 removed file
    [DCC mDecoder.brd, DCC mDecoder.sch]
2026-01-25 Add: Create PinConfig.h for pin configuration definitions
2026-01-25 Add: Create board.txt for attiny85 build extra flags
2026-01-25 Add: Include PinConfig.h for pin configuration definitions
2026-01-25 Remove unused Arduino includes and debug message definitions from DecoderCoreConfig.h
